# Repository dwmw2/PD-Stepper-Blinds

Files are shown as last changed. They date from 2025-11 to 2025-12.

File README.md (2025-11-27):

# PD-Stepper-Blinds



ESPHome-based automatic blind control system using the [PD-Stepper](https://github.com/joshr120/PD-Stepper) controller board by ThingsbyJosh.com.

## Overview

This project provides a complete solution for automating window blinds with precise stepper motor control. It includes 3D-printable mounting hardware, a custom power distribution PCB, and ESPHome configuration for seamless Home Assistant integration.

## Hardware

### Components

- **PD-Stepper Kit** - ESP32-based stepper motor controller (includes board, encoder magnet, aluminium spacer and heatsunk)
- **Stepper Motor** - NEMA 17 or compatible
- **Custom Power PCB** - Distributes power to the PD-Stepper board via spring terminals connected to internal pads
- **3D-Printed Mounting Hardware** - Complete blind mounting assembly
- **M3 Hex Standoffs and Nuts** - For assembly ([example](https://www.amazon.co.uk/dp/B08FZKLYSB))
- **M3 Countersunk Bolts, 15mm and 22.5mm** - For mounting ([example](https://www.amazon.co.uk/dp/B0CPDQJ7ZF))
- **JST-PH 2.0mm Connectors** - 3-pin connectors for power PCB ([example](https://www.amazon.co.uk/dp/B0CDG95RDT))
- **2mm Acrylic Rod** - For light guides ([example](https://www.amazon.co.uk/dp/B0DQ1757SP))

### Power Distribution

Power is supplied through a custom PCB that connects to internal pads on the PD-Stepper board using spring terminals, eliminating the need for external connectors.

## 3D Design

The mounting hardware consists of multiple printed parts that work together to create a complete blind mounting assembly.

### Parts

**Motor Housing and Gear**
- **BasePlate** - Main mounting base
- **Outer** - Outer housing component
- **Inner** - Inner housing component
- **Cover** - Top cover
- **Gear** - Drive gear for blind mechanism

**Installation Template**
- **Motor Cavity Template** - Template for positioning screw holes and motor cutout in the window frame

**PCB Assembly Jig**
- **JigOuter** - Assembly jig outer piece
- **JigSpacer** - Assembly jig spacer (for soldering socket onto PCB)

### Design Files

- **Source File** - `3d-design/BlindMount.FCStd` (FreeCAD format)
- **STL Files** - Individual parts in `3d-design/STL/`
- **3MF Files** - Individual parts in `3d-design/3mf/`

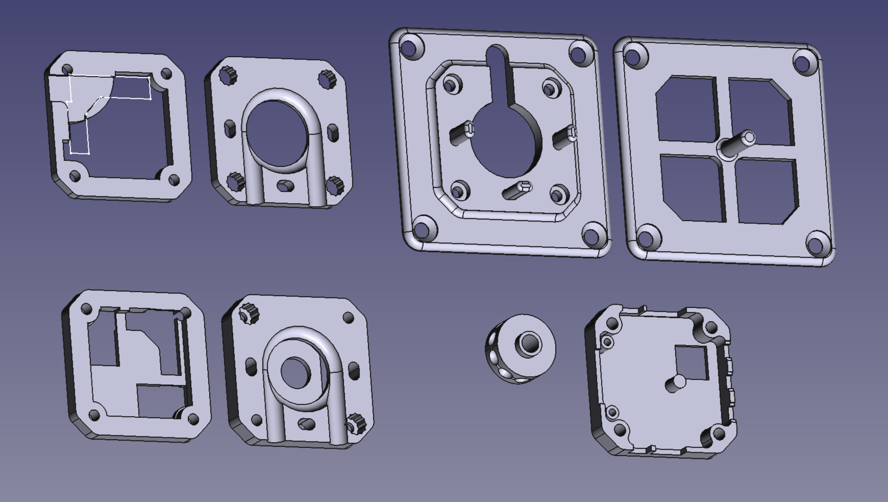
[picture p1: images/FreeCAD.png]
3D Design


## Assembly

### 1. Power PCB Preparation

See [power-pcb/README.md](power-pcb/README.md) for PCB assembly instructions.

| Power PCB | Assembled PCB |
|---|---|
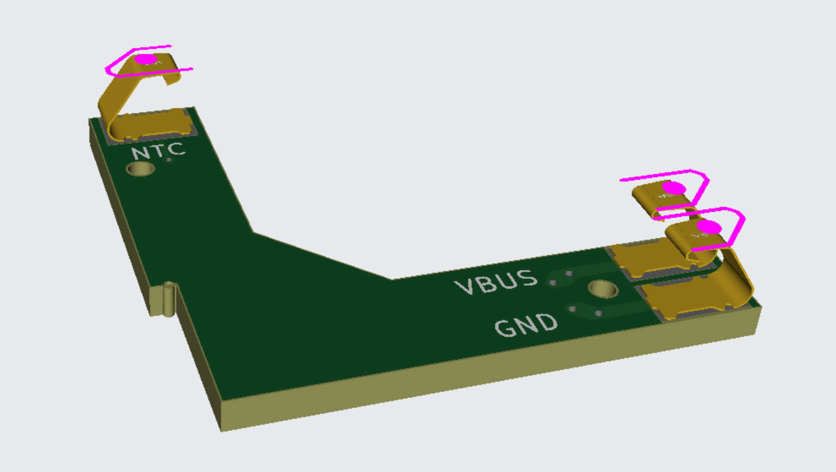
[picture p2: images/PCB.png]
Power PCB
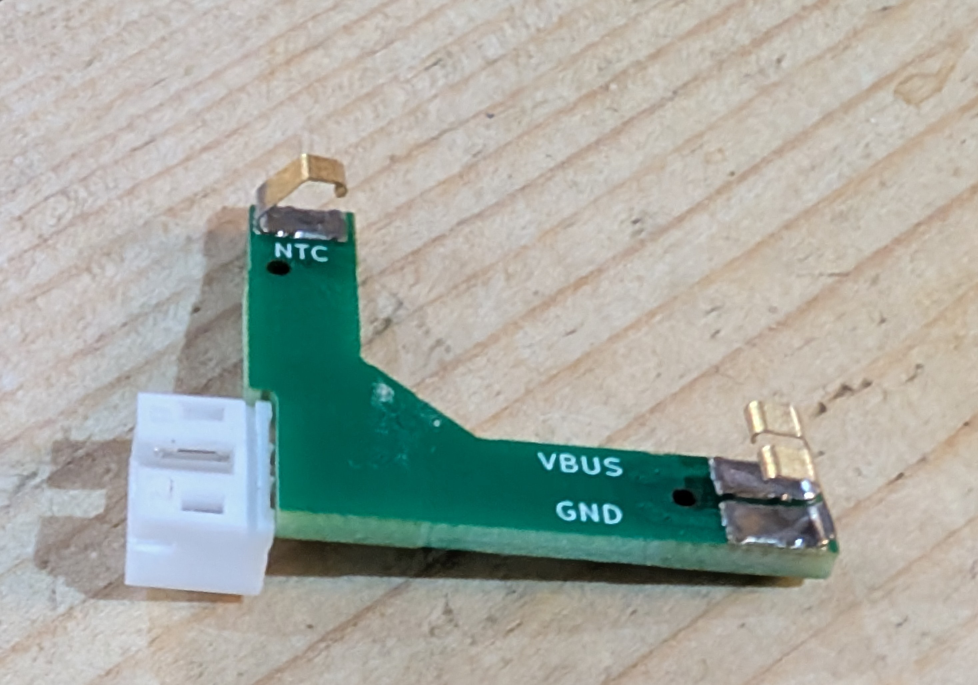
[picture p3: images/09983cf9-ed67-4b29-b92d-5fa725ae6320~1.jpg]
Assembled PCB
|  |  |

### 2. Outer Assembly

- Prepare the 3D-printed Outer piece by pushing two half-width M3 nuts into diagonally opposed holes, then pushing the power PCB into its slot on the other side.
- Attach the PD-Stepper board to the aluminium spacer using the sticky heat transfer pad, and loosely place the Cover piece on top.
- Apply the Outer piece to the back of the PD-Stepper board so that the spring terminals make contact with the power and NTC pads.
- Screw together using two 15mm countersunk bolts.
- Cut sections of the acrylic rod to use as light guides, and push them gently into the holes for the blue and red LEDs.
- Finally, affix the heatsink to the full assembly through the gap in the Cover.

| Exploded View | Bottom | Top |
|---|---|-----|
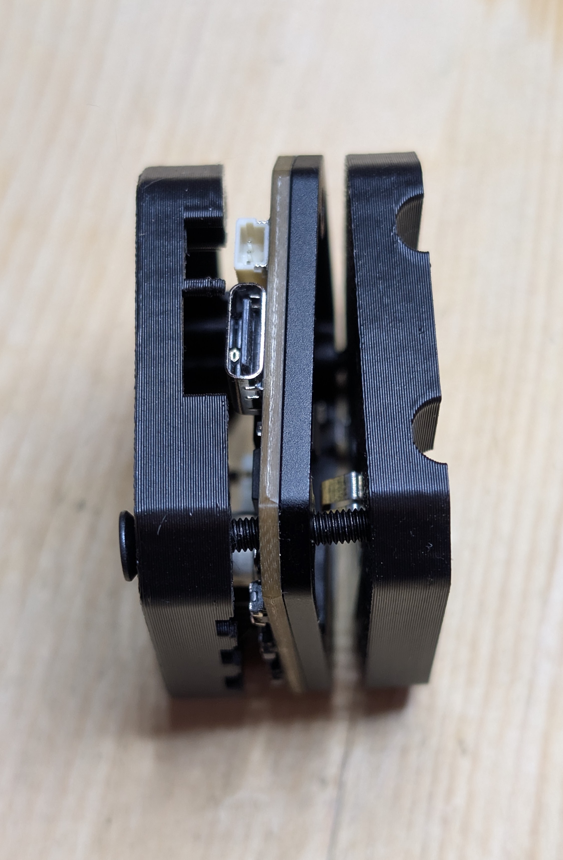
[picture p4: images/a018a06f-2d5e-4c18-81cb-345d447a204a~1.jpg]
Exploded Outer Assembly
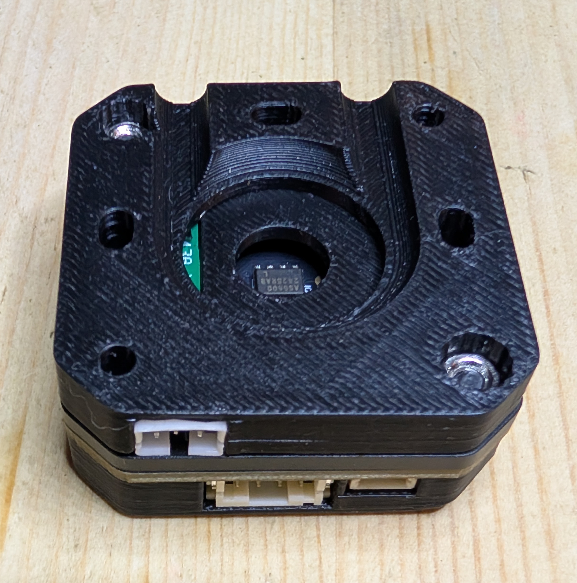
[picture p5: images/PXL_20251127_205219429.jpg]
Completed Outer Assembly - bottom
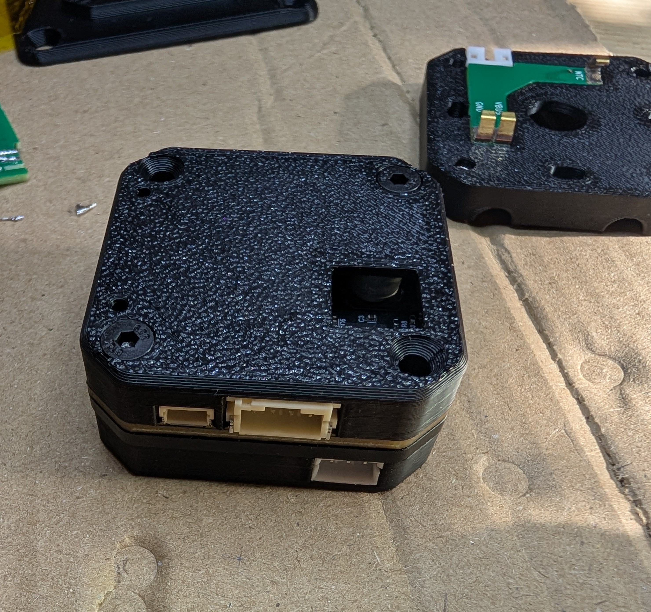
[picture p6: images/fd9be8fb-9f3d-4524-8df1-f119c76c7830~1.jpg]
Completed Outer Assembly - top
|  |  |  |

### 3. Build Motor Cable

- Using JST-PH 2.0 connectors, build a 4-pin to 6-pin cable which works for your motor, matching either the straight-through or crossover cables from the PD-Stepper kit which won't be long enough to reach.
- Test the motor and cable using your completed outer assembly.

### 4. Motor Housing

- Pass the motor cable through the cable hole, then attach the Base Plate to the motor using the hex standoffs. Use two short (5-6mm) standoffs in the corners where the Outer assembly is screwed together, and two longer (8mm) standoffs in the corners which will be used to screw the Inner to this piece.
- You will have to turn the standoffs by a few degrees to the correct orientation such that the Inner piece fits over them. The Inner piece itself can be used as a spanner for that purpose. The Inner piece then pushes over the standoffs and guide posts.
- Offer the Outer assembly up to this to check that it all fits together.

| Aligning the hex standoffs | Motor Assembly |
|---|---|
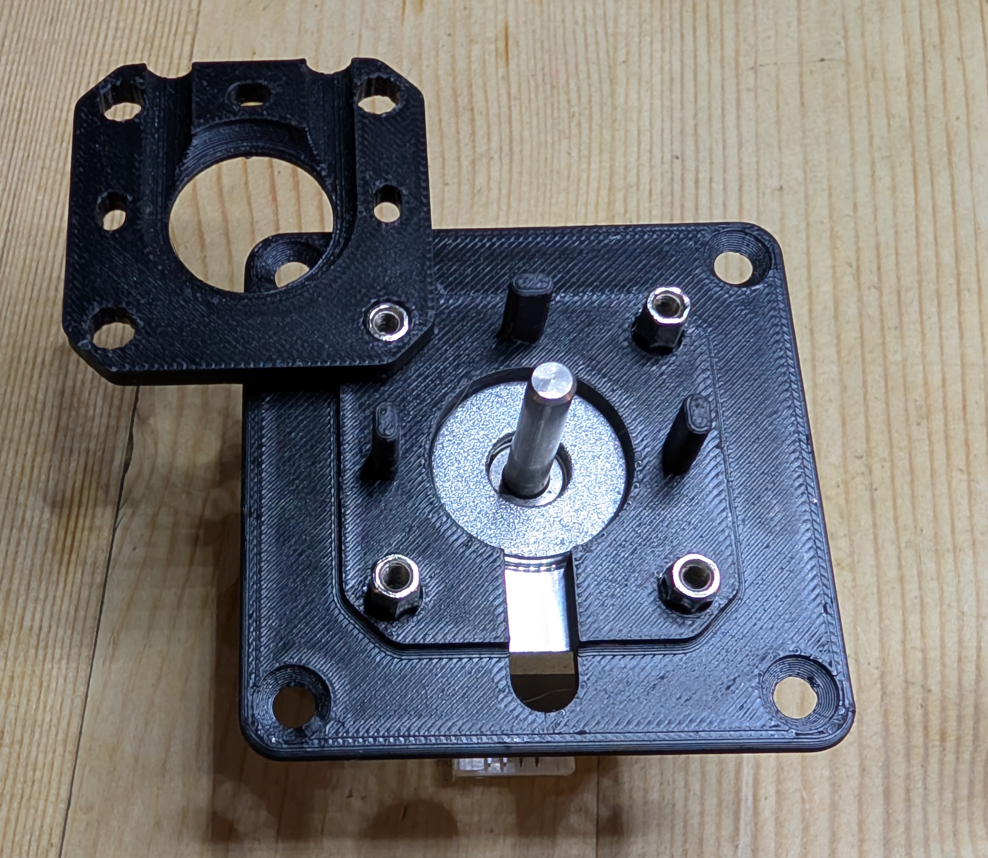
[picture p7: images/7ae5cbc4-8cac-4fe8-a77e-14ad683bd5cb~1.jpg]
Aligning the hex standoffs
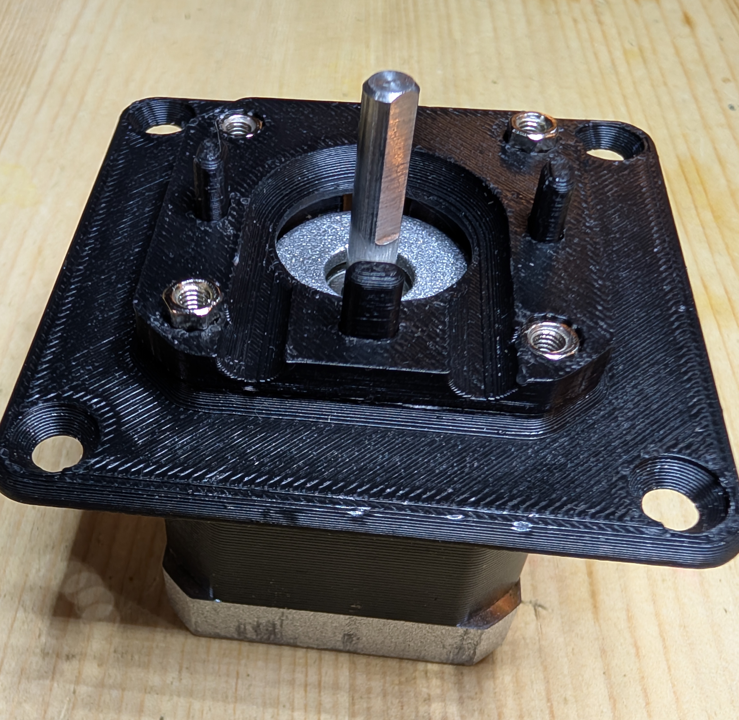
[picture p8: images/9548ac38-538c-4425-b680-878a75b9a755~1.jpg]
Motor Assembly
|  |  |

### 5. Gear Installation

- Push the Gear onto the motor shaft, pushing it fully home until the centre of the Gear is aligned with the centre of the guides in the Inner (and Outer) pieces and the cord will flow freely.
- The centre of the Gear is fully round for 2.5mm at the back and then has a flat part. This is fully parameterised in the spreadsheet in the FreeCAD model, if you need to adjust it or make the Inner piece thicker to allow for a longer shaft.
- You may also need to trim the motor shaft so that there is sufficient space to install the encoder magnet. The easiest way to do this is to install a Gear and then use a Dremel to cut through both Gear and motor shaft at the right point. I kept the motor turning as I did this to ensure a smooth cut.
- Push the encoder magnet from the PD-Stepper kit into the front of the Gear as shown. It should push fully home and be a relatively snug fit. If you have a metallic blind cord, note that the magnet may sometimes prefer attaching itself to the blind cord rather than staying in the Gear where you put it.

| Trimmed gear shaft | Gear with magnet |
|---|---|
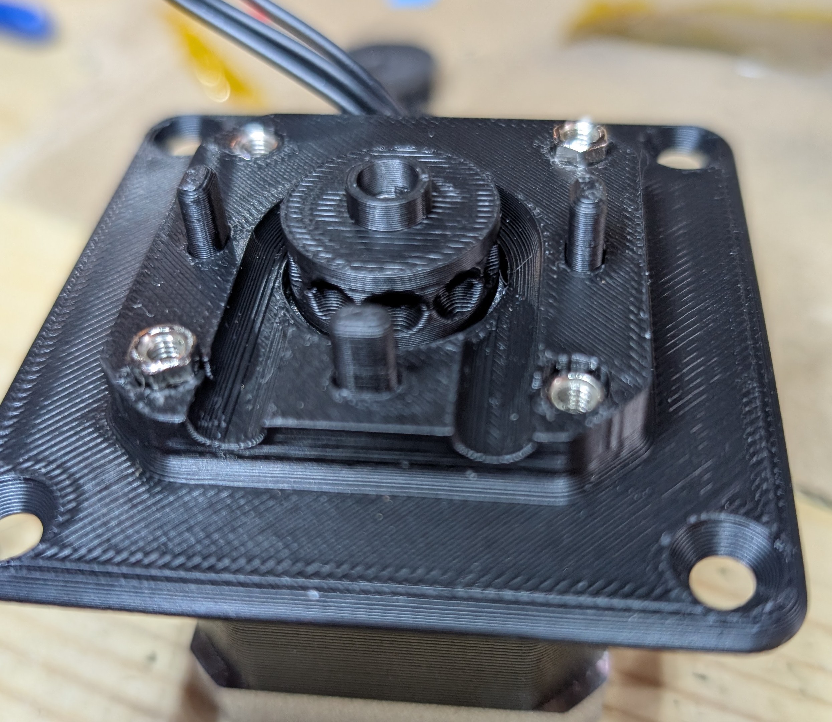
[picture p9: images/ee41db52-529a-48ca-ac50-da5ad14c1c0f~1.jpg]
Trimmed gear shaft
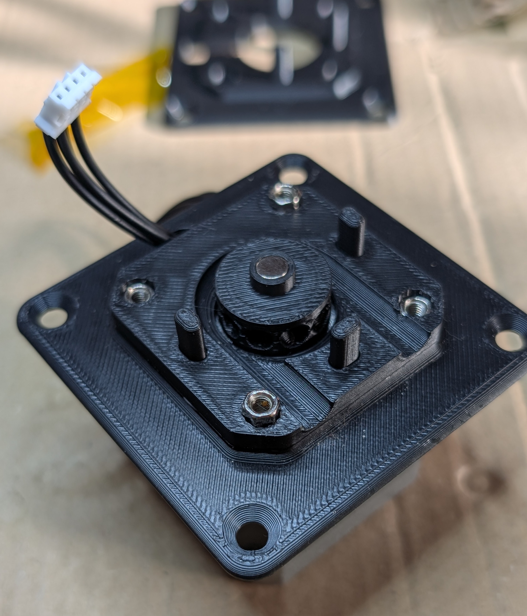
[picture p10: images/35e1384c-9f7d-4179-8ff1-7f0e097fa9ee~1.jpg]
Gear with magnet
|  |  |

### 6. Final Assembly

- Two 22.5mm bolts go through the other corners of the Outer assembly to secure it to the Base Plate, with the blind cord inside. Bolts of that length are hard to come by; you *may* find that 20mm is just about enough, but I used 25mm bolts and the Dremel.
- The 3-pin JST-PH plug is shown connected to the Power PCB in the Outer Assembly. You may prefer to use all black for the visible part, and/or apply heatshrink. As shown in the images, the pinout is:
  - Black: GND
  - Red: +5V to +20V
  - Yellow: Reed switch, closed to GND when the blind is fully open *(optional)*.

| Assembled Units | Connector Wiring |
|---|---|
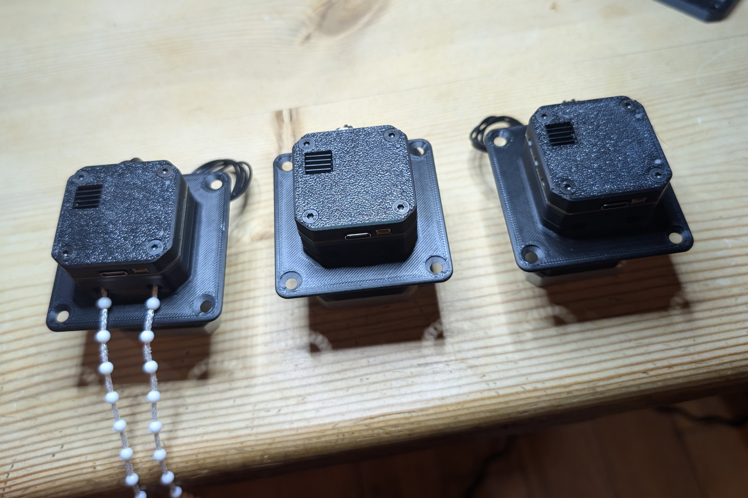
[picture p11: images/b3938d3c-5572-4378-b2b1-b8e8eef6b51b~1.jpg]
Assembled Units
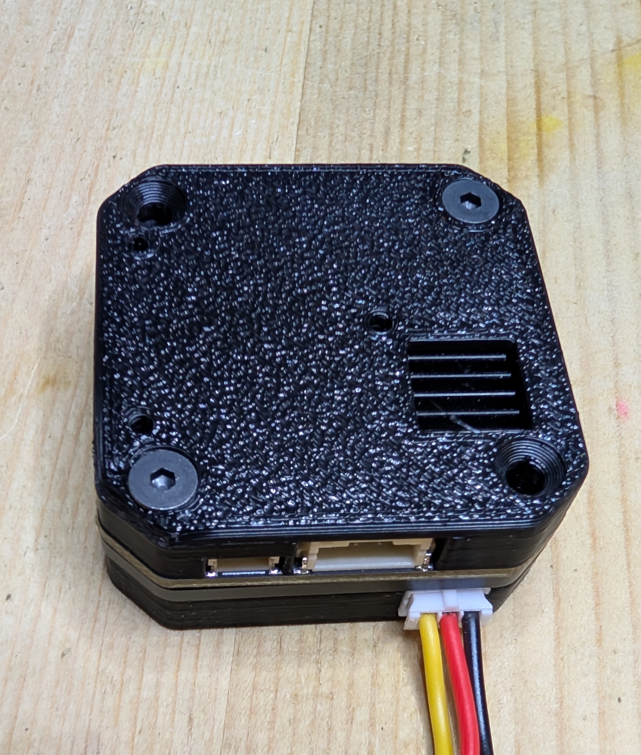
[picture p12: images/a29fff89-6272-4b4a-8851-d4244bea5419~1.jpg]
Connector Wiring
|  |  |

## Installation

For instructions on mounting the completed assembly into your window frame, see [INSTALLATION.md](INSTALLATION.md).

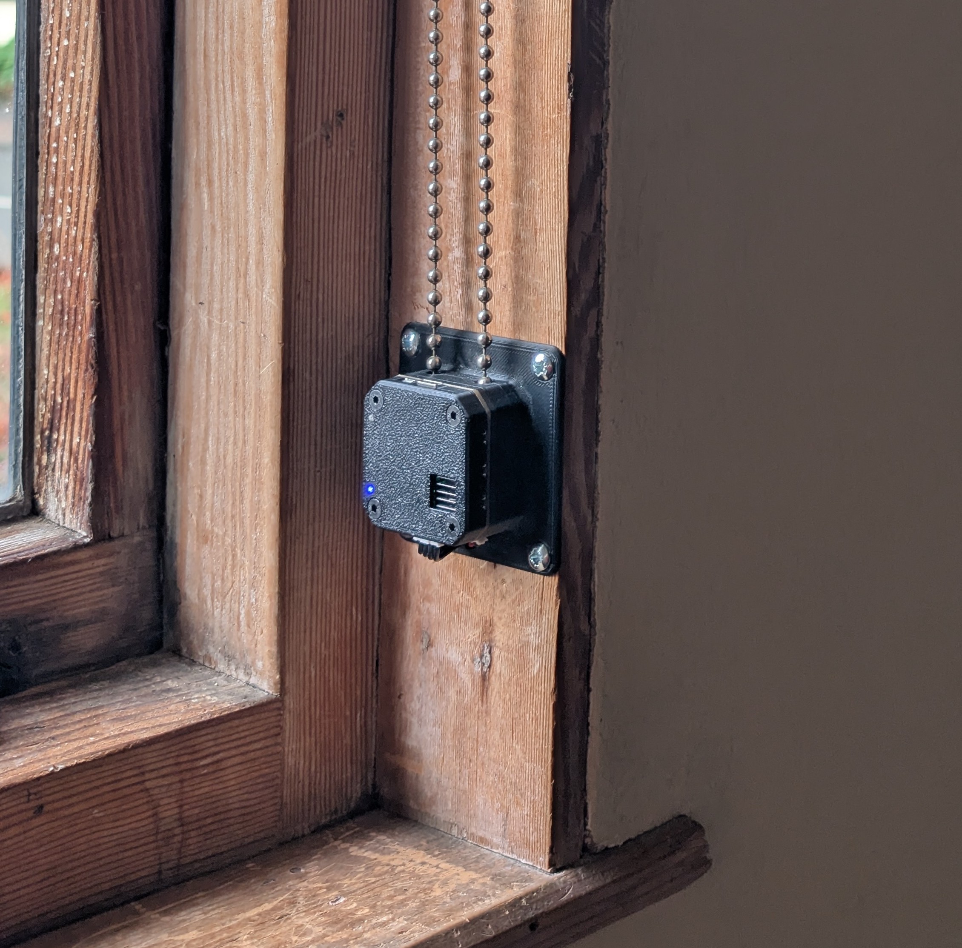
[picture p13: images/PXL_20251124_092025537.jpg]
Installation


## Programming

ESPHome configuration examples are provided in the `esphome/` directory. The `landing-blind-1.yaml` file shows a complete configuration with the following substitutions:

- **name** - Device name for ESPHome and Home Assistant
- **encoder_closed_pos** - Full blinds length in encoder counts (adjust to suit your setup)
- **encoder_direction** - Which direction is towards 'closed' (1 or -1)
- **motor_direction** - Motor direction relative to encoder (1 or -1)
- **microsteps** - Microstepping setting for the stepper driver
- **run_current** - Motor run current (e.g., "100m" for 100mA)
- **max_speed** - Maximum motor speed
- **stallguard_threshold** - StallGuard threshold for stall detection
- **pd_voltage** - Power delivery voltage (unused)

On power-up, the controller will assume that the blinds are open. The first time it is asked to open the blinds, it will perform a rehoming operation, running at half-speed until it stalls. It will close the blinds at sunset, and open the blinds at 07:30AM or sunrise, whichever is later.

You can tweak the current, speed and stallguard settings to suit your blinds and motor, so that the stall is detected correctly. The motor_direction may differ for supposedly identical installations, if your motor cables are wired differently. Some notes on calibration are in the top of the [`blind.yaml`](esphome/blind.yaml) file.

The third pin on the power connector is for a reed switch, which connects that GPIO pin to ground when the blind is fully open. This is not necessary, because rehoming works well with properly calibrated stall detection anyway. One thing that a reed switch would allow is for the device to be *sure*, on startup, that it is at the home position and to initiate a rehoming if not. Rehoming on startup is disabled because when starting from the home position, the immediate stall... well, isn't immediate enough, and is noisy.

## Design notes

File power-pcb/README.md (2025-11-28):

# Power PCB

The custom power distribution PCB is an optional component that provides two key features:

- **Internal Power Delivery** - Supplies power directly to internal pads on the PD-Stepper board via Harwin S1761-42R spring terminals, bypassing the USB-C connector
- **Reed Switch Connection** - Provides a connector for a reed switch to detect when the blinds are fully closed

### Design Files

KiCad project files are located in the `power-pcb/` directory. Gerber and drill files for fabrication are available in `power-pcb/Gerber/`.

You can assemble this yourself, but the spring terminals are hard to solder manually. There are plenty of PCB assembly services which will do it for you; I happened to use JLCPCB. For a walk-through of the JLCPCB ordering process for the uninitiated, see [JLCPCB.md](JLCPCB.md).

Power PCB

## Assembly

The power PCB is designed to make contact with the back of the PD-Stepper board, using the terminals shown.

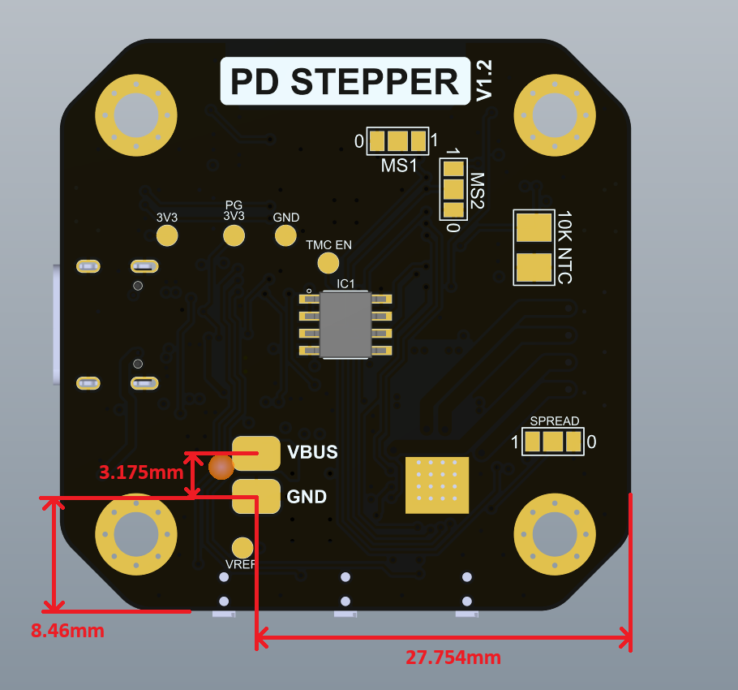
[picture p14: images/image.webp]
Power PCB Terminals


The JST-PH socket is fitted at right angles to the board with its pins laying flat on the copper, so manufacturers like JLCPCB won't be able to build that. Using the Jig as shown to position the socket and PCB, solder them by hand. Don't do it with the PD-Stepper board in place like in the picture. Sandwich the PCB and socket between the Jig parts and screw it together to hold it in place while you solder.

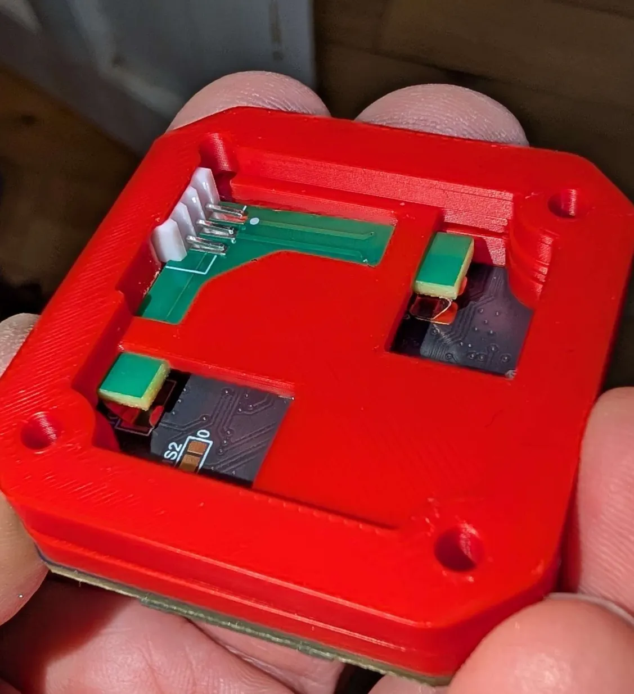
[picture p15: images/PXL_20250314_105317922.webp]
PCB Jig


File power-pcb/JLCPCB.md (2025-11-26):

# JLCPCB Assembly Instructions

## Ordering Process

### Step 1: Prepare Gerber Files
- Create a file `Gerber.zip` containing the contents of the `Gerber/` directory

### Step 2: Create a PCB Assembly project
- Login to JLCPCB account
- Navigate to [https://jlcpcb.com/pcb-assembly](https://jlcpcb.com/pcb-assembly) and click 'Get Started'
- Select 'Add gerber file' and upload the Gerber.zip file
- Check 'PCB Assembly' near the bottom
- Select Tooling holes: Added by Customer, and Confirm Parts Placement: Yes

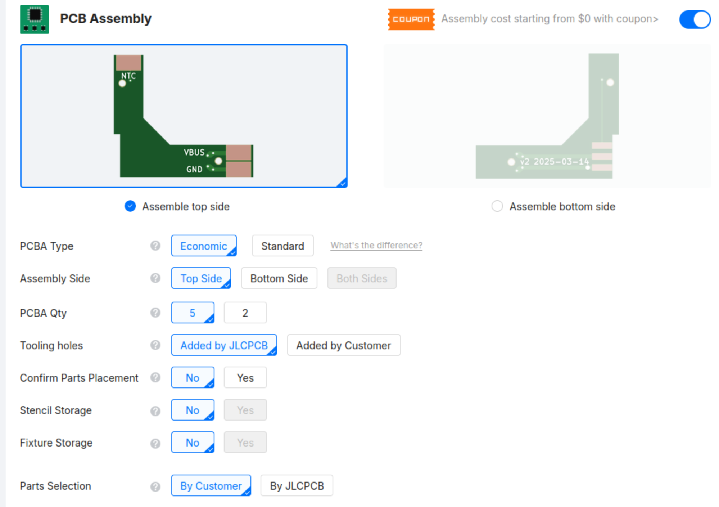
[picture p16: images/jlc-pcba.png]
JLCPCB Assembly Settings


- Click 'NEXT' on the right hand side

### Step 3: Upload BOM
- Click 'Bill of Materials' then 'Add BOM File', and upload [jlcbom.csv](jlcbom.csv)
- Click 'Add CPL File' and upload [jlccpl.csv](jlccpl.csv)
- Click 'Process BOM and CPL'
- It'll say "No part selected" despite the BOM explicitly containing the JLCPCB part number
- Click 'Search' and it'll show you the only matching part. Click 'Select' on it
- Review the placement of the components, which should appear as below, and click 'NEXT'

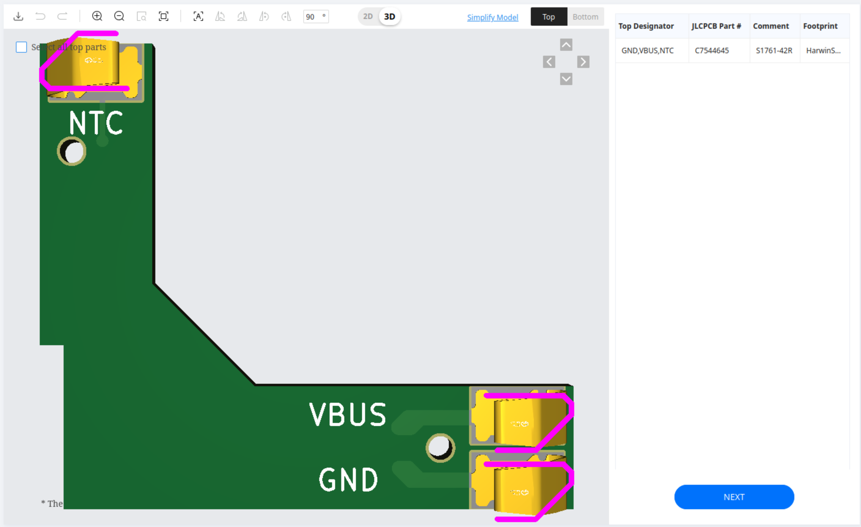
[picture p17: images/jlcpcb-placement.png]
Component Placement


### Step 4: Checkout
- Select the item in your shopping cart and check out

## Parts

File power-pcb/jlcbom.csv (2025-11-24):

Comment | Designator | Footprint | JLCPCB Part Number
S1761-42R | GND,VBUS,NTC | Harwin S1761-42R | C7544645

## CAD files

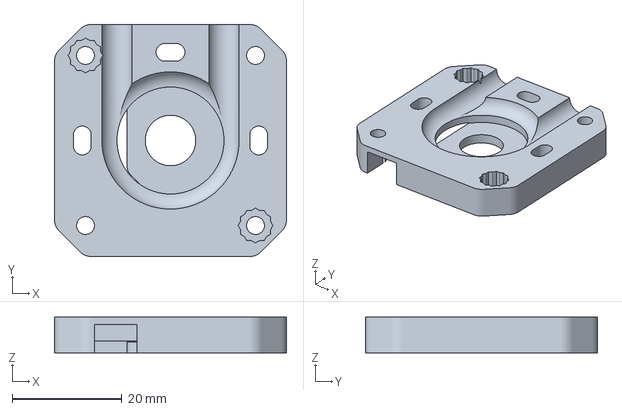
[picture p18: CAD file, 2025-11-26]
3d-design/3mf/BlindMount-Outer.3mf
42.3 x 42.3 x 6.50 mm

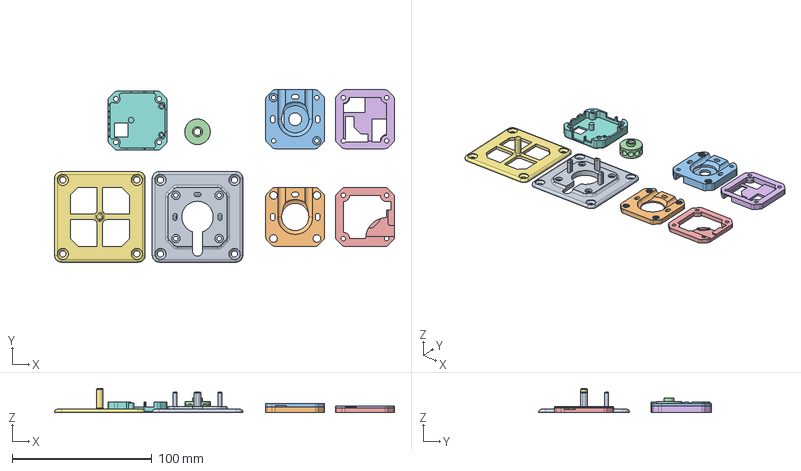
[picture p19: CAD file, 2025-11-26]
3d-design/BlindMount.FCStd
243.7 x 123.7 x 17.5 mm
Body_Outer
Gear
Body_JigSpacer
Body_JigOuter
Motor Cavity Template
Body_Cover

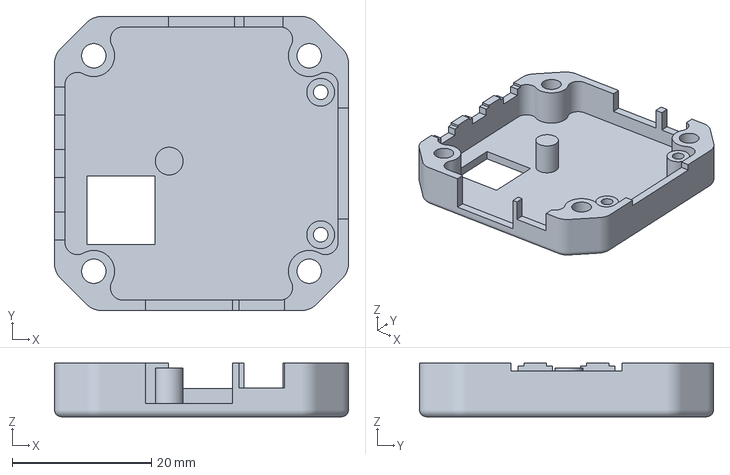
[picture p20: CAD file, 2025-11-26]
3d-design/3mf/BlindMount-Cover.3mf
42.3 x 42.3 x 7.70 mm

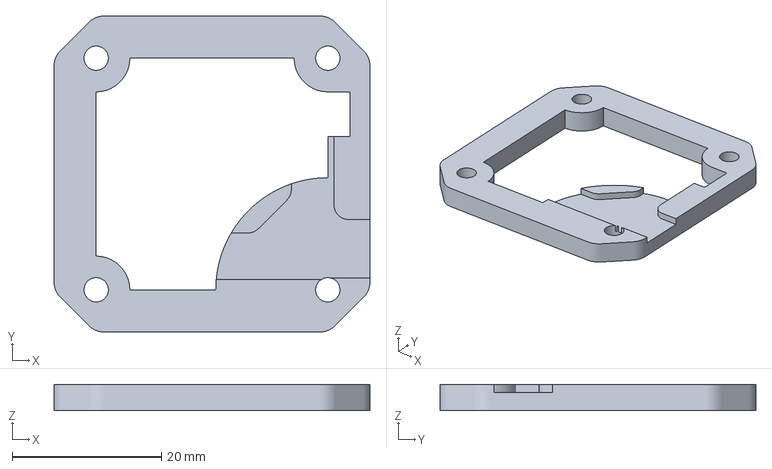
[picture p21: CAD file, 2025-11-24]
3d-design/3mf/BlindMount-JigSpacer.3mf
42.3 x 42.3 x 3.50 mm

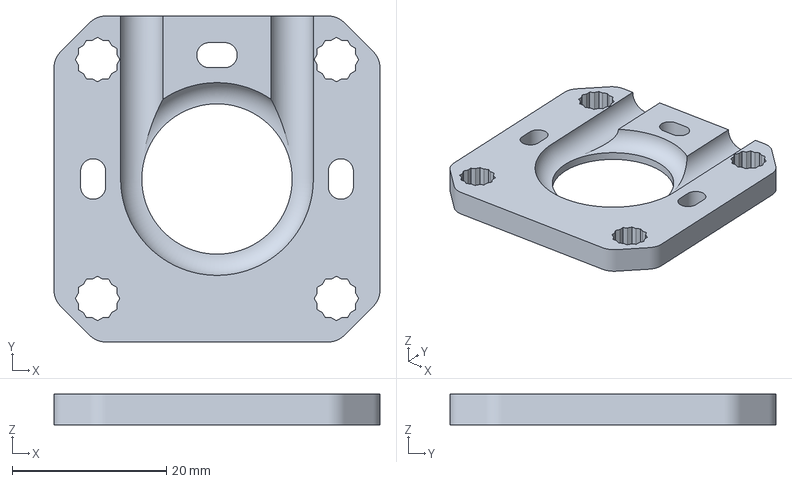
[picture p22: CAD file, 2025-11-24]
3d-design/3mf/BlindMount-Inner.3mf
42.3 x 42.3 x 4.00 mm

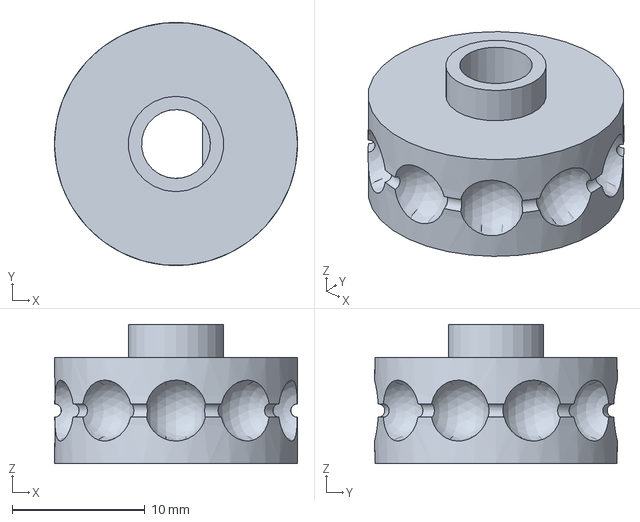
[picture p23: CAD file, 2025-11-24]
3d-design/3mf/BlindMount-Gear.3mf
18.3 x 18.3 x 10.5 mm

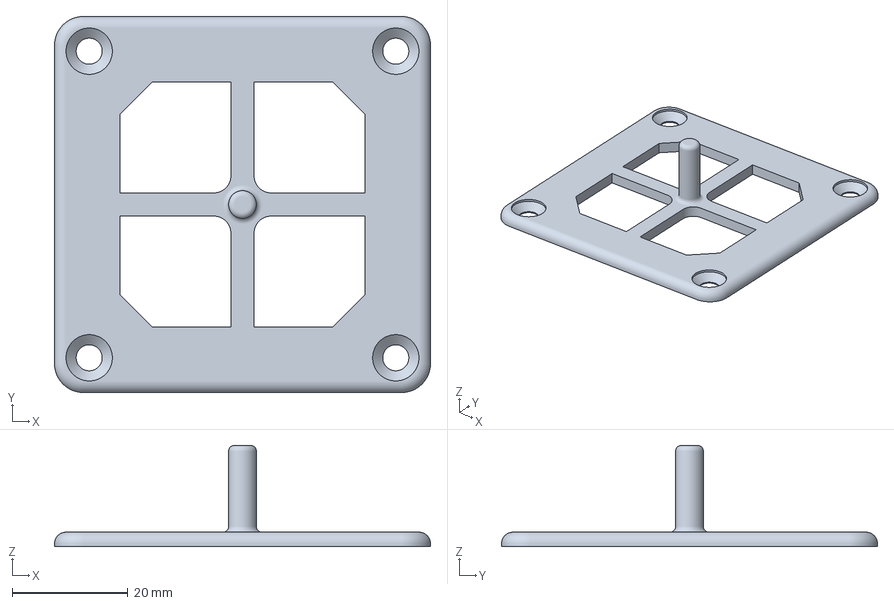
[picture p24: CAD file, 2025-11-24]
3d-design/3mf/BlindMount-Motor Cavity Template.3mf
65.0 x 65.0 x 17.5 mm

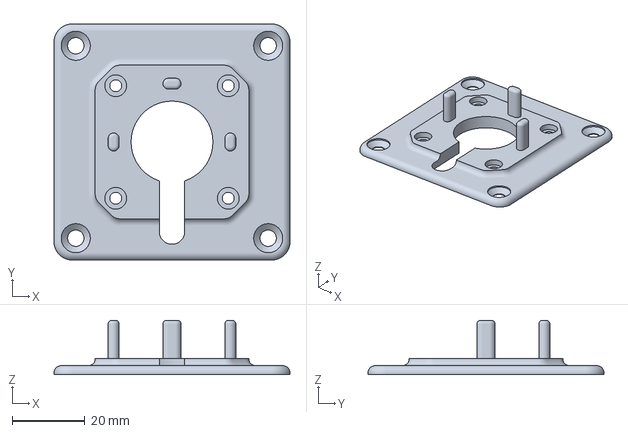
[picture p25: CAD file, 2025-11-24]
3d-design/3mf/BlindMount-BasePlate.3mf
65.0 x 65.0 x 15.0 mm

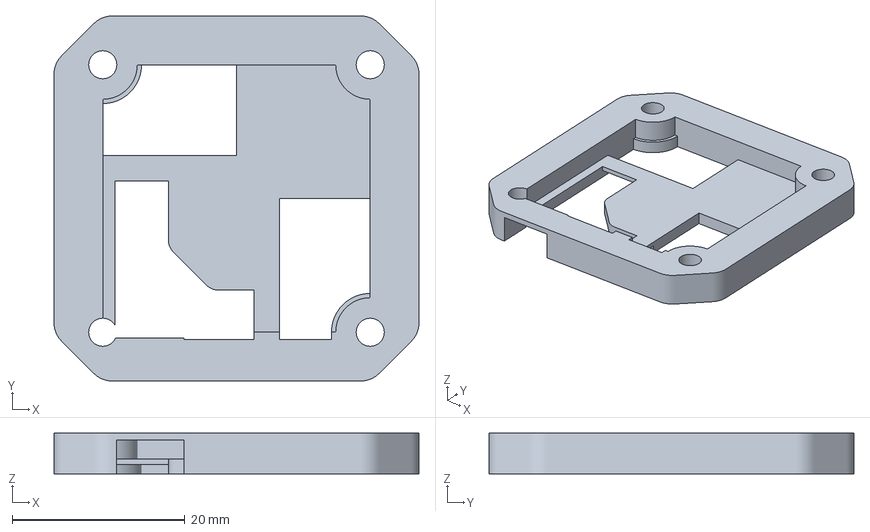
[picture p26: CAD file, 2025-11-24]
3d-design/3mf/BlindMount-JigOuter.3mf
42.3 x 42.3 x 4.75 mm

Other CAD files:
3d-design/STL/BlindMount-BasePlate.stl
3d-design/STL/BlindMount-Cover.stl
3d-design/STL/BlindMount-Gear.stl
3d-design/STL/BlindMount-Inner.stl
3d-design/STL/BlindMount-JigOuter.stl
3d-design/STL/BlindMount-JigSpacer.stl
3d-design/STL/BlindMount-Motor Cavity Template.stl
3d-design/STL/BlindMount-Outer.stl

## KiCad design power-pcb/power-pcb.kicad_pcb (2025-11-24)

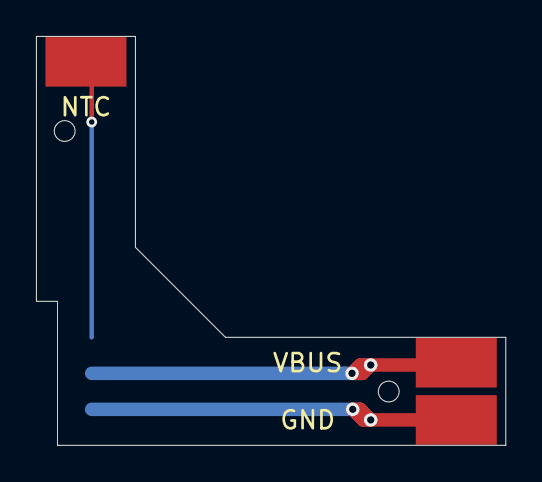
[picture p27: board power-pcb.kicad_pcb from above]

Board: 2 copper layers, 26.1 x 22.7 mm, 4 parts (1 on the bottom side), 3 nets.

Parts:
GND: Conn_01x01_Pin; HARWIN_S1761-46R
J1: Conn_01x03_Pin; JST_S3B-PH-SM4-TB_LF__SN_
NTC: Conn_01x01_Pin; HARWIN_S1761-46R
VBUS: Conn_01x01_Pin; HARWIN_S1761-46R

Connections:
GND: GND.1, J1.1
unnamed: J1.3, NTC.1
VBUS: J1.2, VBUS.1

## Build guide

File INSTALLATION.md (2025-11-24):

# Installation

## 1. Position and Mark

Mount a gear on the Motor Cavity Template and find where it sits on the side of the window frame, and mark the location to cut. The blind cord doesn't need to be tight; a little bit of slack is fine.

## 2. Cut Motor Cavity

Cut the hole for the motor in the window frame and ensure that the motor can sit completely inside so that its face is flush with the frame, with space for the motor wires.

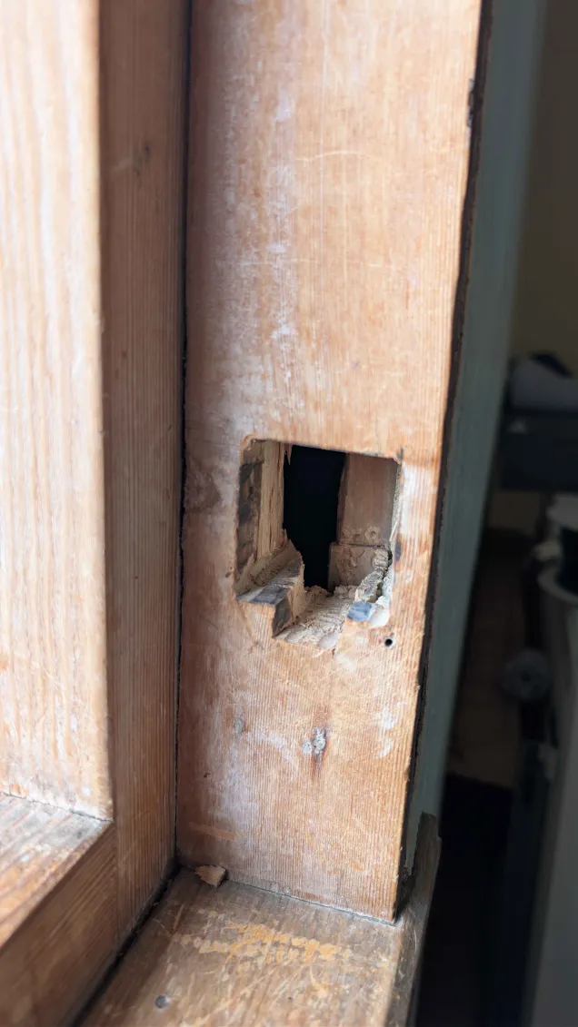
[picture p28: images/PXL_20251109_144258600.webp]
Motor Cavity Cut


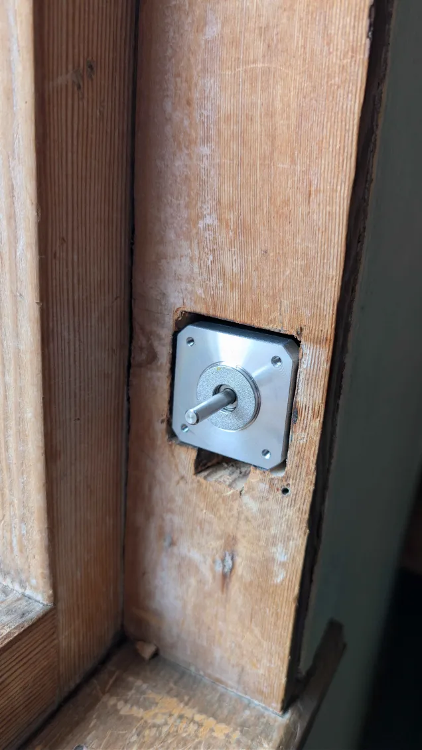
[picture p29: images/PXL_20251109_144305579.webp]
Motor Flush with Frame


## 3. Route Power Cable

Feed the power cable through the wall cavity to reach the motor from within the wall.

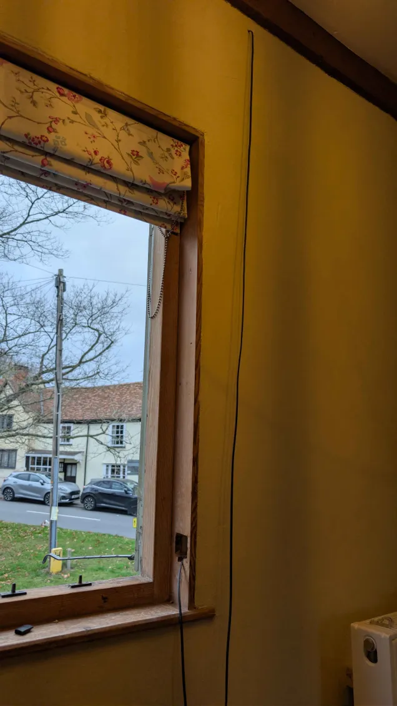
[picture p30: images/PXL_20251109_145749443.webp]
Power Cable Routing


## 4. Terminate Power Cable

Bring the power cable through the gap in the base plate alongside the motor cable, and terminate it in a 3-pin JST-PH plug. Vcc is the middle pin of the 3-pin plug, and GND is the pin closest to the edge. An optional reed switch can be connected between GND and the NTC pin, which is closest to the centre of the assembly.

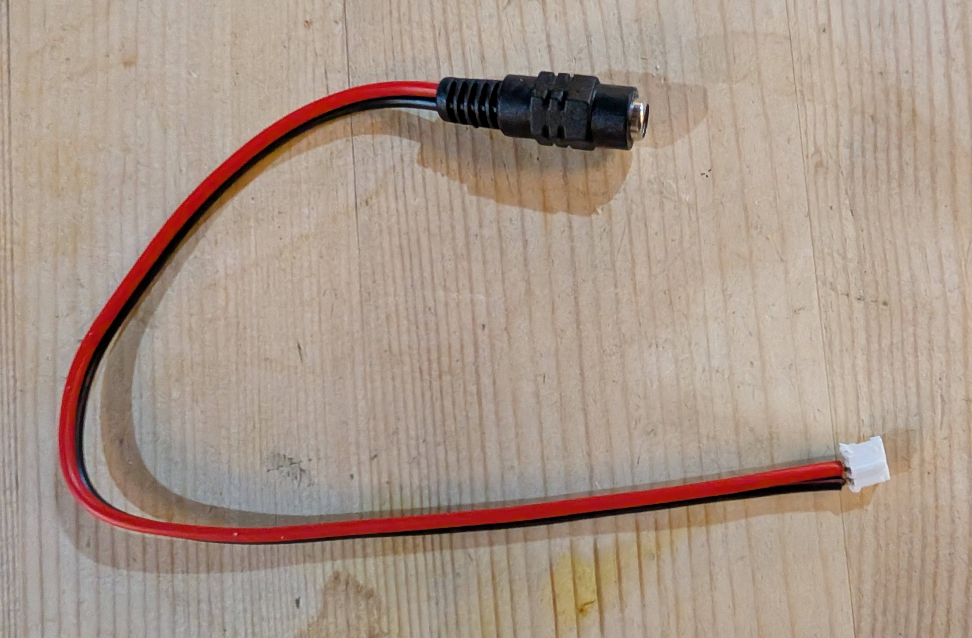
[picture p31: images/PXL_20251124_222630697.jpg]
Power Connector


## 5. Connect Assembly

Fit the blind cord to the complete assembly and connect the power cable as shown.

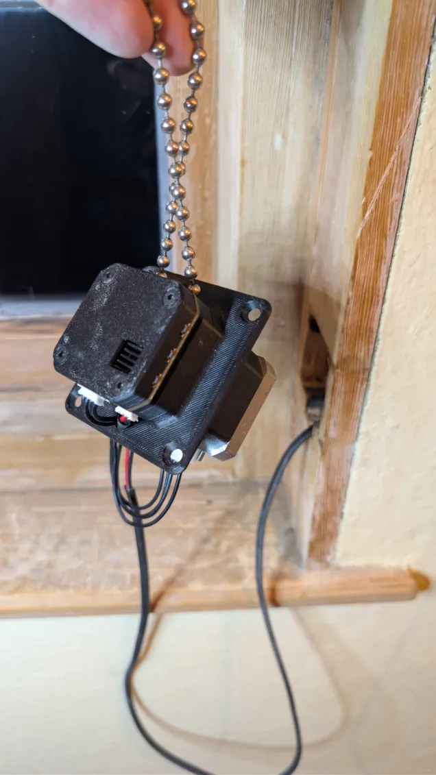
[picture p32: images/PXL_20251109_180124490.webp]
Assembly with Connections


## 6. Mount Assembly

Mount the complete assembly in the wall cavity and screw in the four corners with self-tapping screws.

Final Installation

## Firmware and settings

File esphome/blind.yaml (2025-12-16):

# Based on https://github.com/joshr120/PD-Stepper/blob/main/Software/ESPHome/PD-Stepper-Blinds-Advanced.yaml
# (GPLv3)

# Tuning...
#
# Total motor speed (steps/s / microsteps) should be fast enough to be useful,
# but slow enough not to be too noisy. Too fast may also make the cord skip on
# the gear when it should be stalling.
#
# If steps/s is too high (regardless of microsteps), the Power Good light randomly
# cuts out and the board resets (with three different power supplies). Decreasing
# run_current doesn't seem to make any difference to that.
#
# StallGuard should be sensitive (high) enough to stop quickly when it reaches
# the end stop (although that's less important with the reed switch hooked up),
# but low enough not to trigger if starting up in the high-torque region when
# the blind is almost, but not quite fully up.
#
# Making the re-homing run at half speed helps with the latter, as does lower
# acceleration.
#
# Increasing microsteps decreases torque, as does decreasing the current. This
# affects the StallGuard settings.
#
# Microsteps (between 1 and 4 at least) don't seem to make any noticeable difference
# to the smoothness of operation.
#
# Setting standstill_mode to coil_short_ls prevents high back EMF if someone
# manually turns the blinds.

esp32:
  board: esp32-s3-devkitc-1
  framework:
    type: esp-idf
    version: recommended

esphome:
  name: ${name}
  platformio_options:
    board_build.flash_mode: dio
    upload_speed: 921600
  on_boot:
    - lambda: |
           auto t = id(sntp_time).now();
           ESP_LOGE("on_boot", "%svalid %04d-%02d-%02d %02d:%02d:%02d, is_dst %d",
           t.is_valid() ? "": "in", t.year, t.month, t.day_of_month,
           t.hour, t.minute, t.second, t.is_dst);
    - tmc2209.configure:
        microsteps: ${microsteps}
        interpolation: true
        tcool_threshold: 400
    - tmc2209.stallguard:
        threshold: ${stallguard_threshold}   #set lower if stall gaurd triggering too often
    - tmc2209.currents:
        ihold: 0
        tpowerdown: 0
        iholddelay: 0
        # irun: 16
        run_current: ${run_current}  #Set your desired current here (800m = 800mA, 1 = 1A etc.)
        standstill_mode: coil_short_ls

     # set PD voltage    # 5V  9V  12V  15V  20V
     #  CFG1             # 1   0    0    0    0
     #  CFG2             # -   0    0    1    1
     #  CFG3             # -   0    1    1    0
    - lambda: |-
         int voltage = ${pd_voltage}; // 5, 9, 12, 15 or 20.
         bool cfg1 = false, cfg2 = false, cfg3 = false;
         if (voltage == 5) {
            cfg1 = true;
         } else if (voltage == 9) {
            // all off;
         } else if (voltage == 12) {
            cfg3 = true;
         } else if (voltage == 15) {
            cfg2 = cfg3 = true;
         } else if (voltage == 20) {
            cfg2 = true;
         } else ESP_LOGE("USB-PD", "Invalid voltage %dV selected", voltage);
         id(CFG1_pin).set_state(cfg1);
         id(CFG2_pin).set_state(cfg2);
         id(CFG3_pin).set_state(cfg3);

    - delay: 0.5s
    - lambda: id(sensored_home_pos) = id(encoder)->get_state();  # Set the home position to power on position
    # - button.press: home

wifi:
  power_save_mode: none
  networks:
    - ssid: !secret wifi_ssid
      password: !secret wifi_pw

network:
  enable_ipv6: true

# Log too much, and the encoder can miss revolutions.
logger:
  level: INFO
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

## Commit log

2025-11-24 initial import
    [BlindMount-BasePlate.3mf, BlindMount-BasePlate.stl, BlindMount-Cover.3mf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]
2025-11-24 Clarify PD-Stepper kit contents
2025-11-24 Move power PCB documentation to subdirectory
2025-11-24 Rename step 2 to 'Outer Assembly'
2025-11-24 Clarify diagonal bolt placement in outer assembly
2025-11-24 Add standoff orientation instructions to motor housing
2025-11-24 Add 2mm acrylic rod to components list
2025-11-24 Add light guide installation to outer assembly
2025-11-24 Add power connector pinout and reed switch details
2025-11-24 Add power connector pinout image
2025-11-24 Add tuning note for motor settings
2025-11-24 Add note about motor_direction variation
2025-11-25 Add reed switch explanation to programming section
2025-11-25 Improve assembly instructions and add calibration reference
2025-11-25 Convert all assembly instructions to bullet points
2025-11-26 Reimplement cover to avoid importing STL
    Importing and modifying STL annoyed me but was good enough for my own
    use. Now it's published it's even more annoying, *and* the original was
    under GPLv3 so reimplement it.
    [BlindMount-Cover.3mf, BlindMount-Cover.stl, BlindMount.FCStd]
2025-11-26 Remove extra nut cavity in Outer
    It doesn't matter, and actually allows for longer standoffs to be used in
    the base plate for that corner, but it's probably just confusing.
    [BlindMount-Outer.3mf, BlindMount-Outer.stl, BlindMount.FCStd]
2025-11-26 Add JLCPCB assembly ordering instructions
2025-11-27 Reorganize assembly images into compact tables
2025-11-27 Replace Final Assembly image with higher resolution version
2025-11-27 Replace Motor Assembly image with higher resolution version
2025-11-27 Replace Outer Assembly top image with higher resolution version
2025-11-27 Update Motor Assembly image and add Gear with magnet image
2025-11-27 Add Trimmed gear shaft image to Gear Installation section
2025-11-27 Add Assembled PCB image to Power PCB section
2025-11-27 Add Connector Wiring image to Final Assembly section
2025-11-27 Add connector pinout details with nested bullets
2025-11-28 Improve PCB soldering instructions
2025-12-16 Fix for sunrise after 8am
    [blind.yaml]

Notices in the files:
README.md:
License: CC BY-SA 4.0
